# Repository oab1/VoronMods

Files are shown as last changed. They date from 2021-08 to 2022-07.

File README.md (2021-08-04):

# V2 Exhaust Housing (Re-circulating)
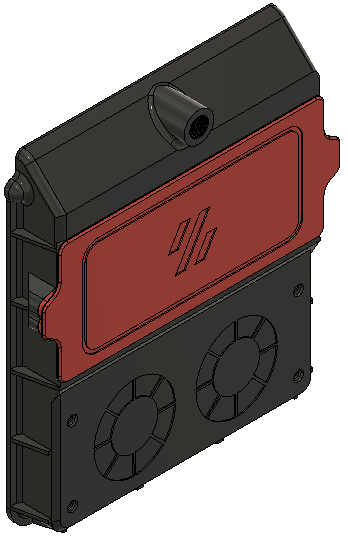
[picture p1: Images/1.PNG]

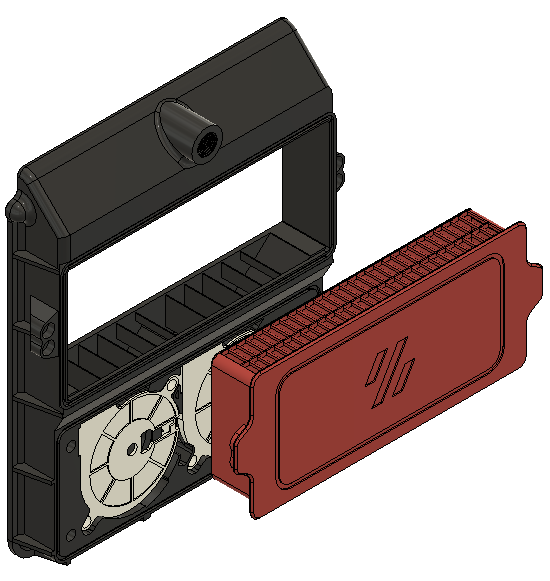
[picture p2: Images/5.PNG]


Modified existing v2.2 exhaust housing to incorporate u/0ndsk4's Nevermore micro re-circulating design. Added BSP fitting for bowden tube from v2.4 and a removable drawer as a filter basket to hold carbon pellets for filtration.

Uses the same 2 5015 Blower fans from the Nevermore, and 4mm activated carbon pellets. Two holes need to be cut into the back panel (1.5" diameter) for the blower fan inlets. The housing works as a good template once it is printed. Housing attaches to back panel with VHB tape, same as v2.2/2.4 designs. Pellets need to be replaced every so often, have heard anywhere from 50-100 hours. Have not run that long myself yet.

## Hardware needed:
- 2x 5015 blower fans (confirmed fitment with Winsin brand, but same as used in nevermore micro)
- 4x 6x3mm magnet (same as used in V2 BOM)
- 6x M3x5x4 heatset inserts
- 4x m3 screws (6-8mm length OK)
- 3M VHB tape
- Approx 200g of 4mm activated carbon pellets, I bought mine here:
https://envirosupply.net/products/4mm-pellet-virgin-coal-activated-carbon-charcoal-for-vapor-filtration-1-lb-bag

## Nevermore micro:
Based on original design from 0ndsk4:
https://github.com/0ndsk4/VoronUsers/tree/0ndsk4/printer_mods/0ndsk4/Nevermore_Air_Filter/Nevermore_Micro

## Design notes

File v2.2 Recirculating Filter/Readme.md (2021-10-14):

# Rear Panel Mounted Re-circulating Filter
Codename: FannyPack (a modified version of the Nevermore Micro Duo) 

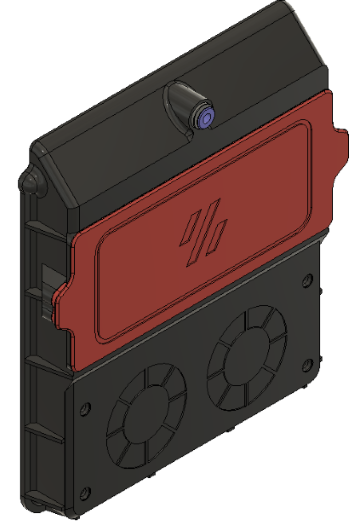
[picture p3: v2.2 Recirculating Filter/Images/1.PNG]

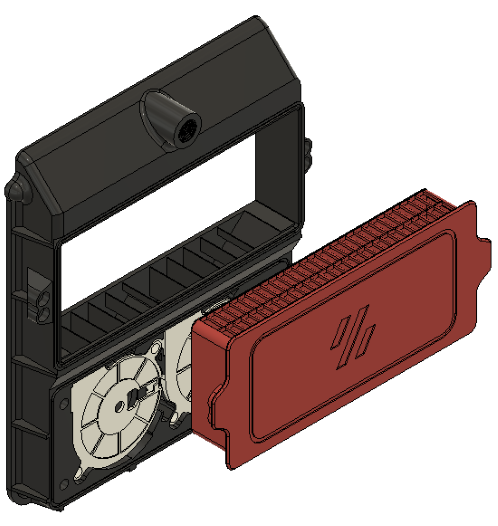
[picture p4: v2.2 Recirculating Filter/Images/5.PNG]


Modified existing v2.2 exhaust housing to incorporate u/0ndsk4's Nevermore Micro Duo:
- Uses the same 2 5015 Blower fans and 4mm activated carbon pellets. 
- Two holes need to be cut into the back panel (1.5" diameter) for the blower fan inlets. 
- The housing works as a good cutting template once it is printed. 
- Housing attaches to back panel with VHB tape
- Removable drawer as a filter basket to hold carbon pellets for filtration.
- Two fitting options for bowden tube: (1) 1/8" BSP adapter (2) EASUN Push Fitting adapter

I recommend printing the housing with at least 3 perimeters and about 15% infill. More infill than that is pretty overkill.

## Hardware needed:
- 2x 5015 blower fans (confirmed fitment with Winsin brand, but same as used in nevermore micro)
- 4x 6x3mm magnet (same as used in V2 BOM)
- 6x M3x5x4 heatset inserts
- 4x m3 screws (6-8mm length OK)
- 3M VHB tape
- Approx 200g of 4mm activated carbon pellets, I bought mine here:
https://envirosupply.net/products/4mm-pellet-virgin-coal-activated-carbon-charcoal-for-vapor-filtration-1-lb-bag

## Nevermore micro:
Based on original design from 0ndsk4:
https://github.com/0ndsk4/VoronUsers/tree/0ndsk4/printer_mods/0ndsk4/Nevermore_Air_Filter/Nevermore_Micro

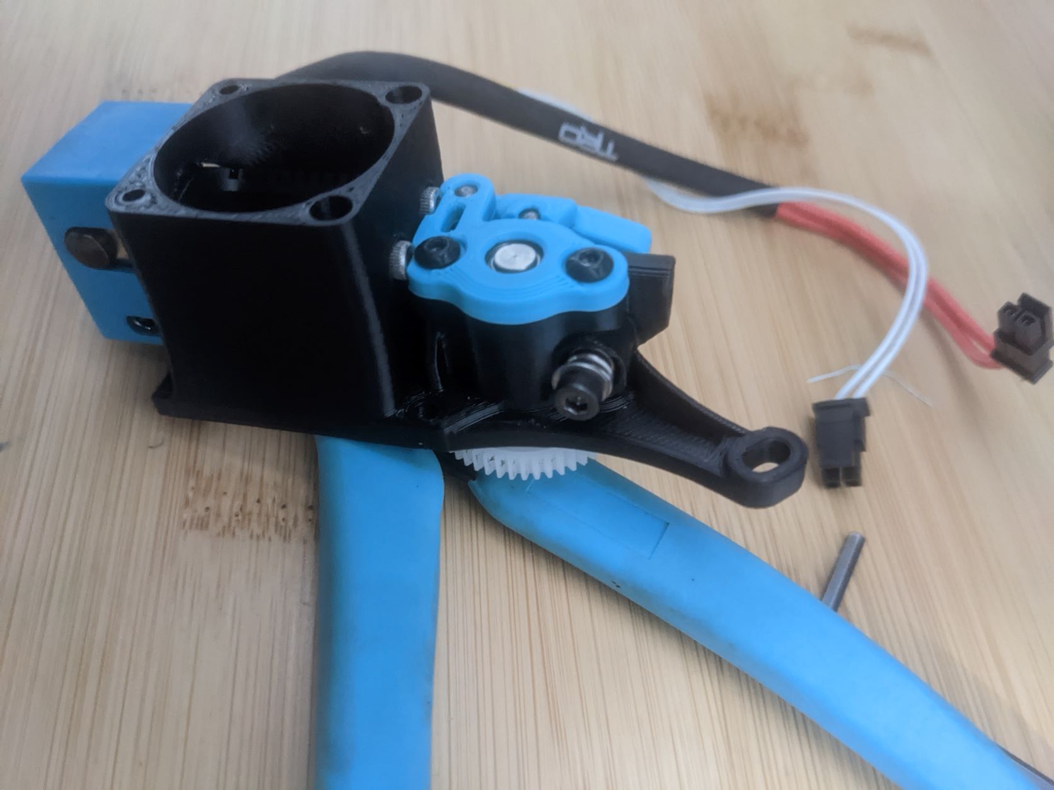
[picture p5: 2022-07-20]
v2.2 Recirculating Filter/Images/PXL_20220714_225406142.MP.jpg

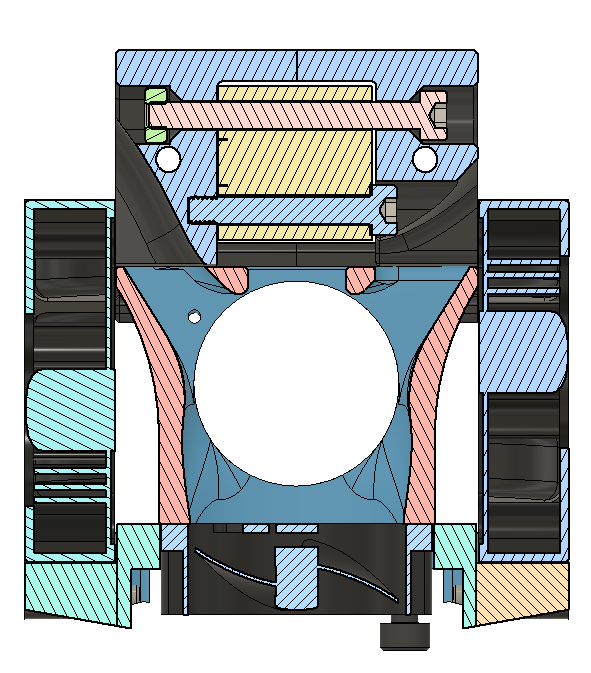
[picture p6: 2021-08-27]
v2.2 Sherpa Mini Toolhead/Images/v1/Exhaust Flow Path.PNG

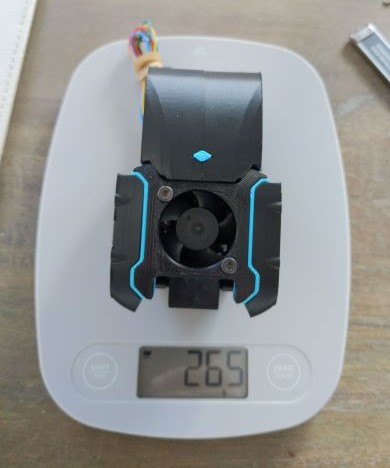
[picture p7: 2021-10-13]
v2.2 Sherpa Mini Toolhead/Images/scale_weight.PNG

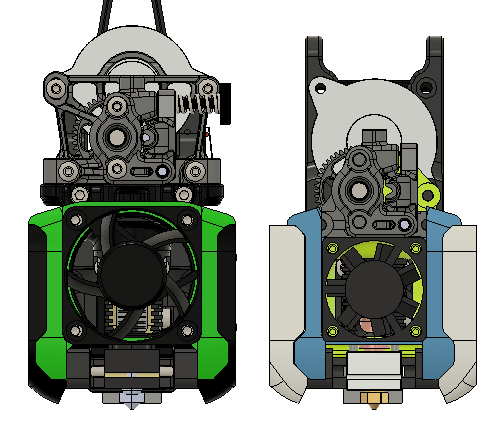
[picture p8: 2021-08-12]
v2.2 Sherpa Mini Toolhead/Images/v1/size compare.png

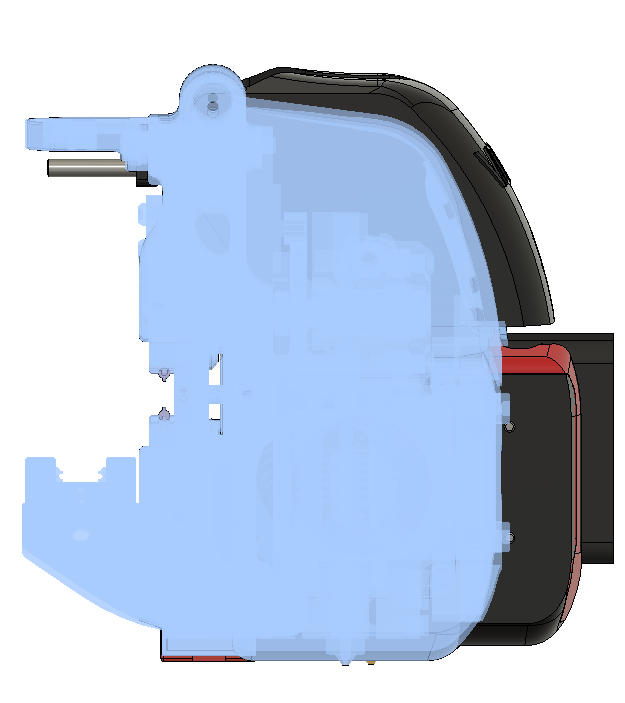
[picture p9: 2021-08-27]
v2.2 Sherpa Mini Toolhead/Images/size compare 2p2 original.PNG

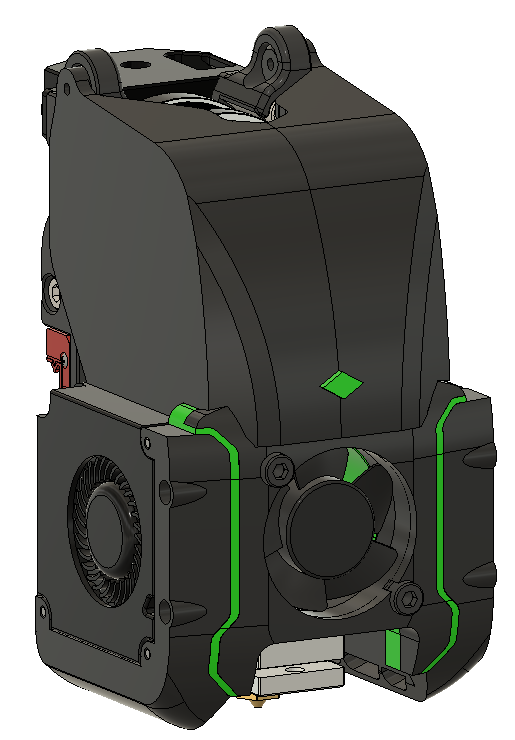
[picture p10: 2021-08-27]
v2.2 Sherpa Mini Toolhead/Images/v1/annex-green.PNG

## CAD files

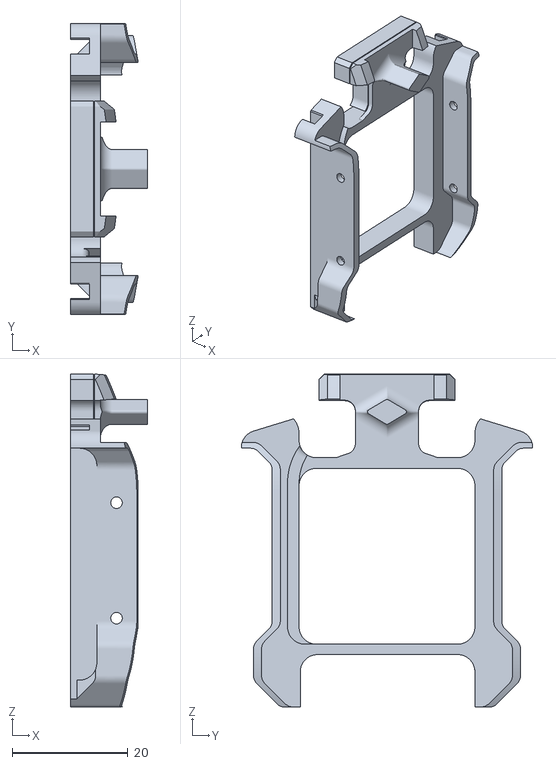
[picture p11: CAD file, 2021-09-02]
v2.2 Sherpa Mini Toolhead/STL/fan_back_plate.stl
13.3 x 50.4 x 57.6

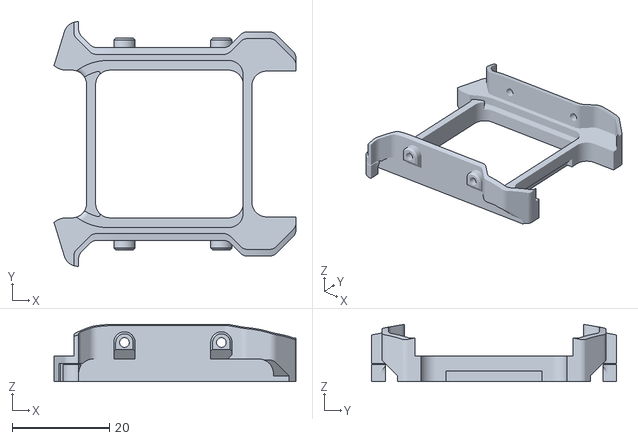
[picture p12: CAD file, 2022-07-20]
v2.2 Toolhead/STL/Tronhead RC2/annex redoubt + huvud specific/fan_back_plate.stl
49.8 x 50.4 x 11.8

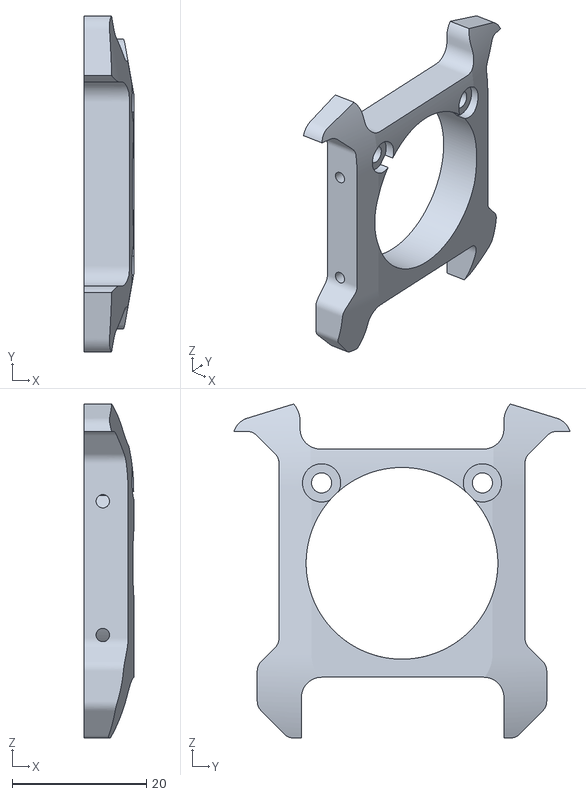
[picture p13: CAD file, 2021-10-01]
v2.2 Toolhead/STL/Tronhead RC2/annex redoubt specific/fan_front_plate.stl
7.39 x 50.1 x 49.8

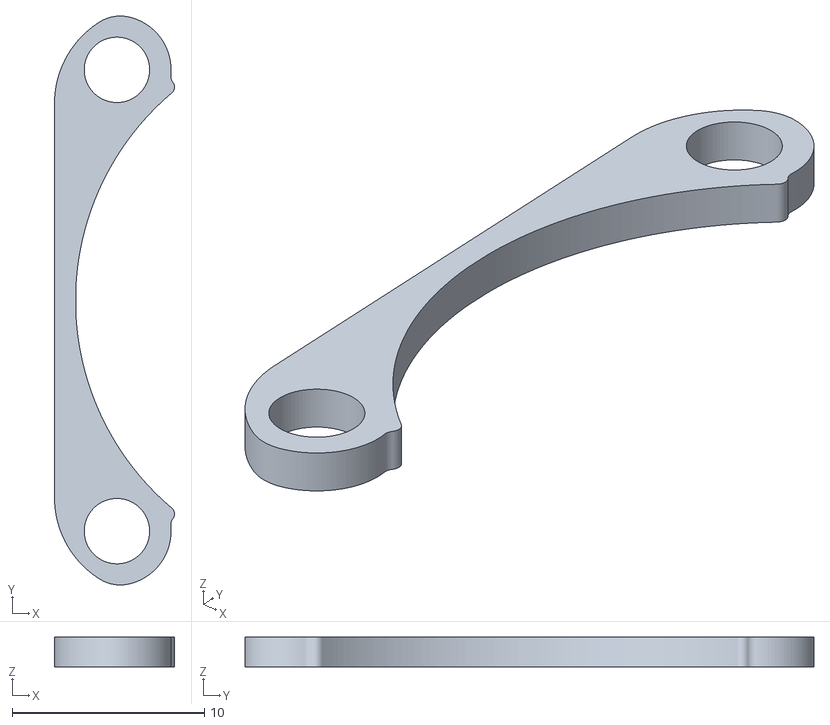
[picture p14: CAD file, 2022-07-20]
v2.2 Toolhead/STL/Tronhead RC2/spacer.stl
6.25 x 29.6 x 1.55

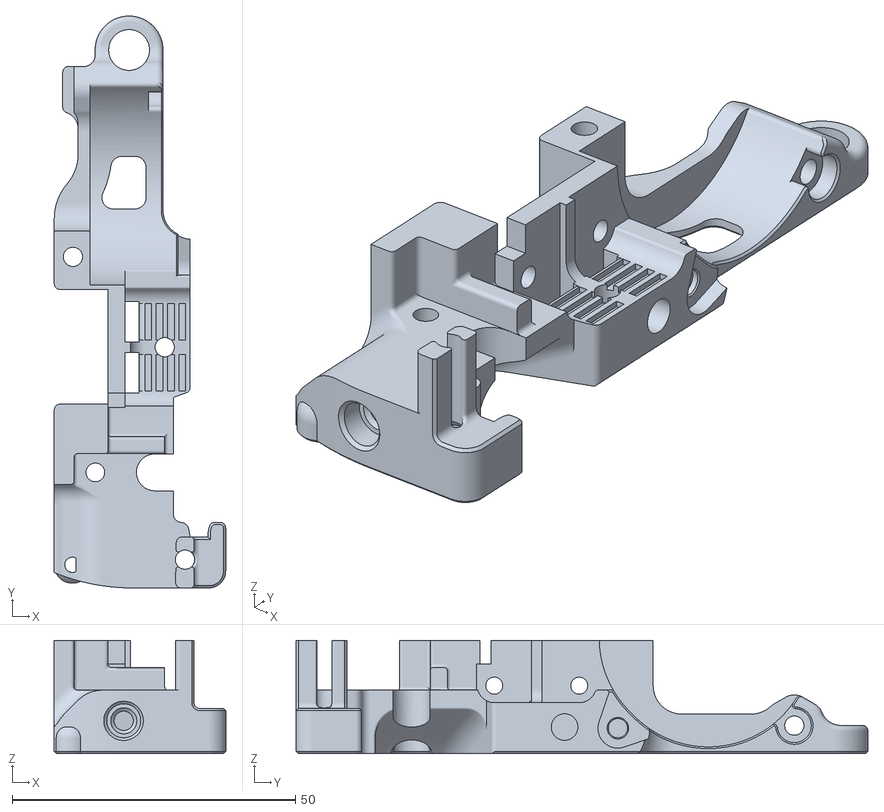
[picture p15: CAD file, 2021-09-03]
v2.2 Toolhead/STL/Tronhead RC2/voron 2.4 specific/x-carriage-omron-mgn9h-single (R).stl
30.3 x 100.9 x 20.0

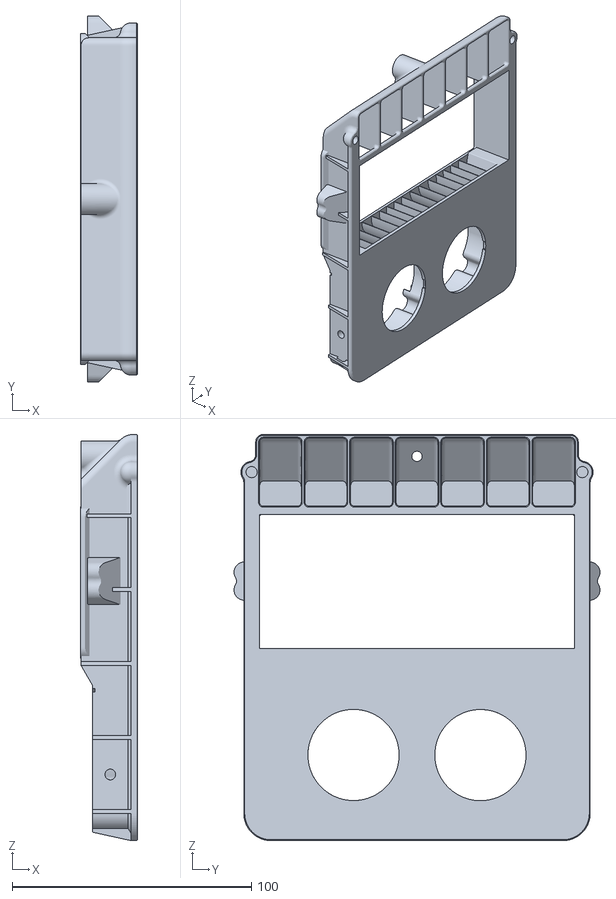
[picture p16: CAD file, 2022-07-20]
v2.2 Recirculating Filter/STL/Housing_rev2 (PushFitting).stl
23.7 x 152.9 x 169.8

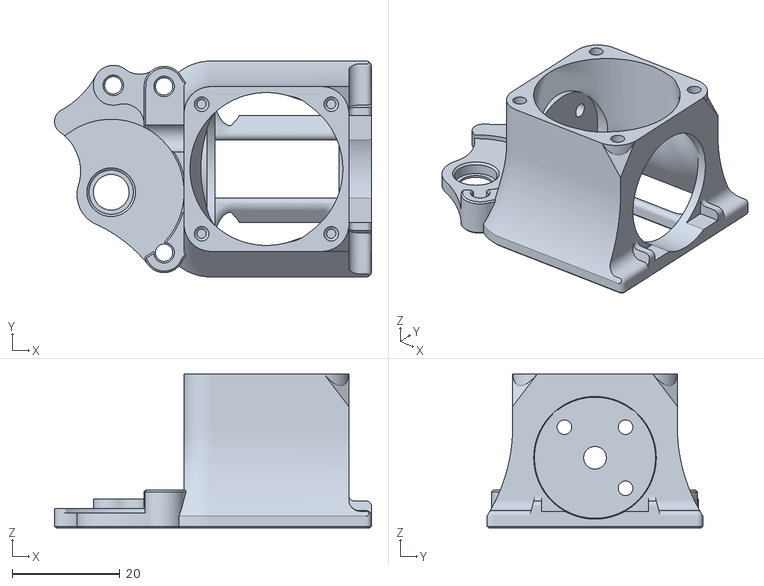
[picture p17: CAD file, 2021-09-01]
v2.2 Sherpa Mini Toolhead/STL/Toolhead Mount_rev2.stl
58.7 x 40.0 x 28.5

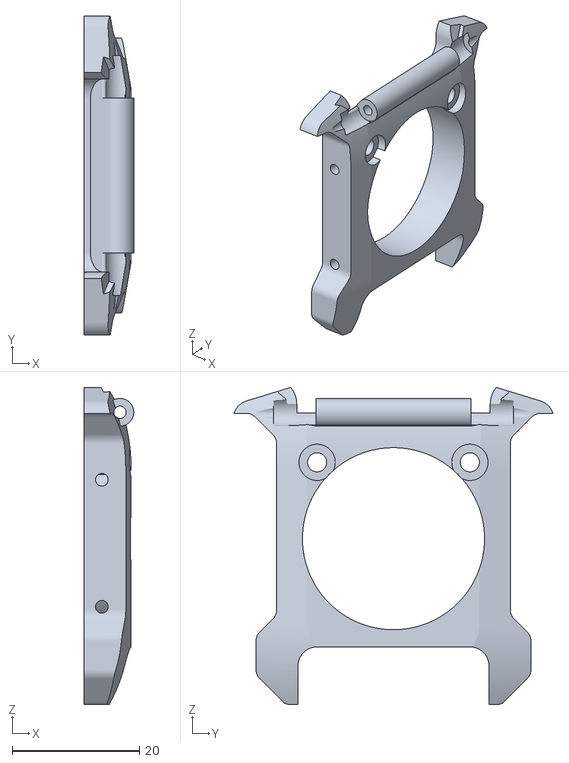
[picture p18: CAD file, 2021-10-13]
v2.2 Toolhead/STL/Tronhead RC2/annex redoubt + huvud specific/fan_front_plate.stl
7.78 x 50.1 x 49.8

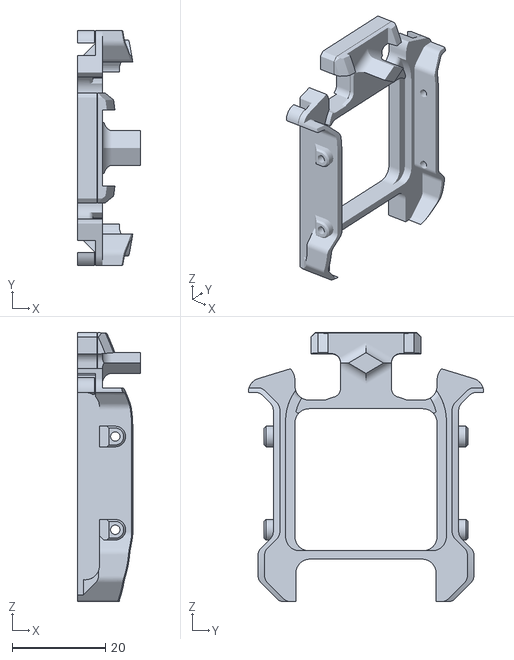
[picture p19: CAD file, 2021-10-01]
v2.2 Toolhead/STL/Tronhead RC2/annex redoubt specific/[a]_fan_back_plate.stl
13.4 x 50.4 x 57.6

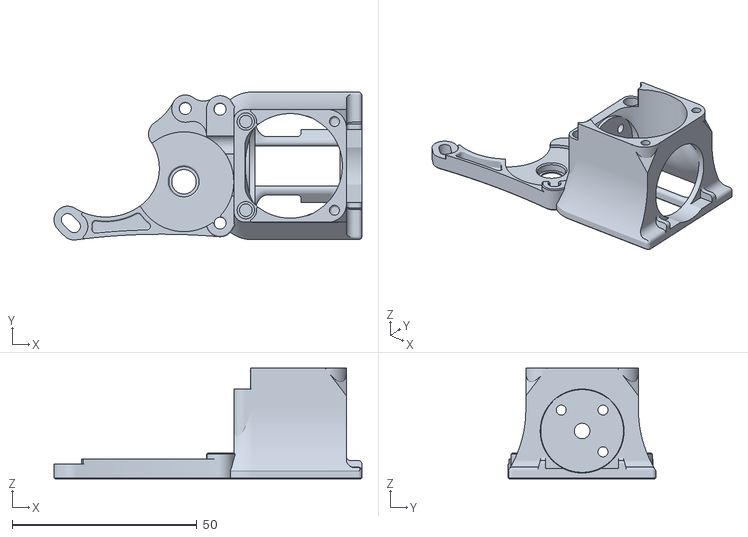
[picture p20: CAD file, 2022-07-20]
v2.2 Toolhead/STL/Tronhead RC2/Toolhead Mount.stl
83.4 x 40.1 x 30.1

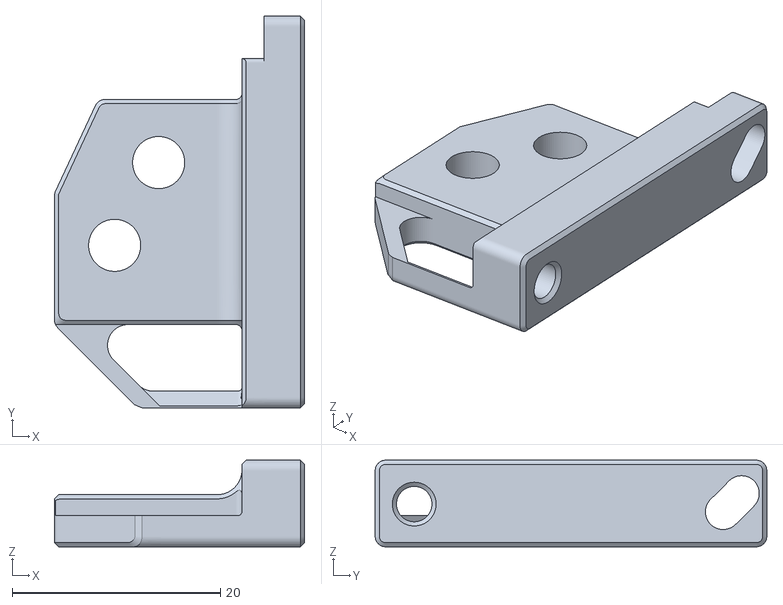
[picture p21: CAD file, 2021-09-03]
v2.2 Toolhead/STL/Tronhead RC2/voron 2.4 specific/1011_china_chain_mount.stl
24.0 x 37.6 x 8.32

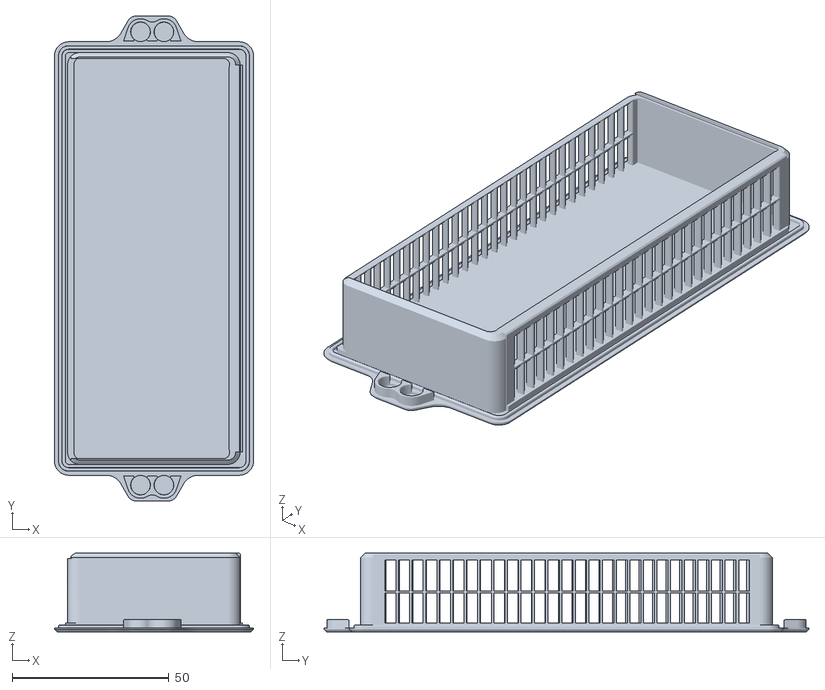
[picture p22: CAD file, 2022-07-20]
v2.2 Recirculating Filter/STL/Basket.stl
63.5 x 154.7 x 25.1

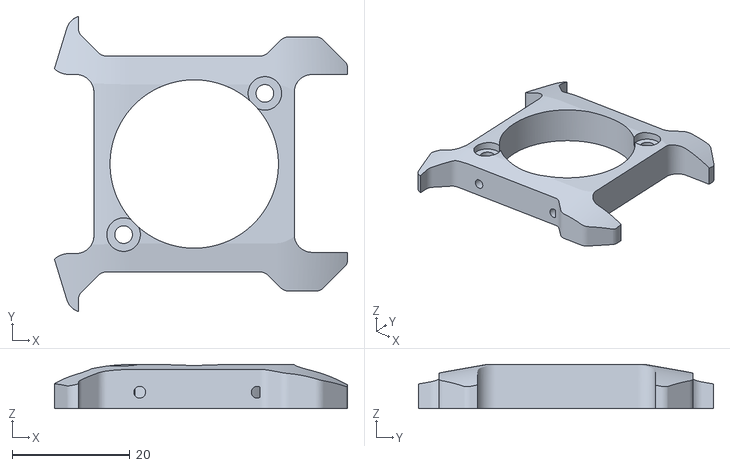
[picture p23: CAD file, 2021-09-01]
v2.2 Sherpa Mini Toolhead/STL/fan_cover_plate.stl
49.8 x 50.1 x 7.49

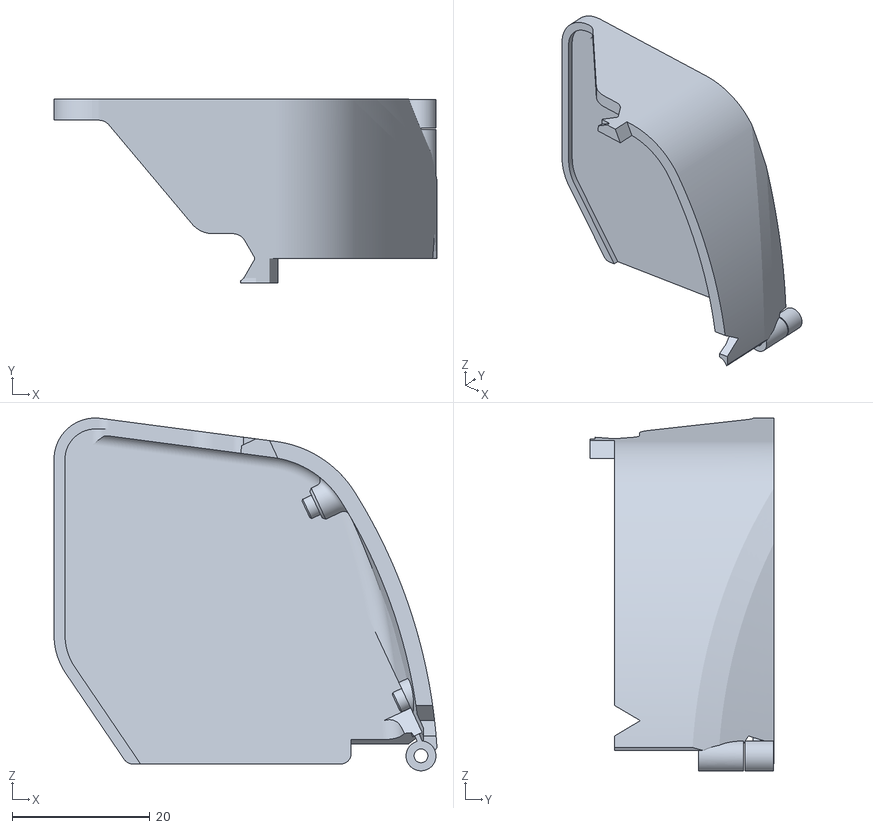
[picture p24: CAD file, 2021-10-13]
v2.2 Toolhead/STL/Tronhead RC2/annex redoubt + huvud specific/Connector_Cover_Right.stl
55.7 x 26.8 x 51.3

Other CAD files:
v2.2 Toolhead/STL/Tronhead RC2/annex redoubt specific/X-Carriage_Left (redoubt umbilical).stl
v2.2 Toolhead/STL/Tronhead RC2/Cooling Fan Duct Right.stl
v2.2 Toolhead/STL/Tronhead RC2/voron 2.4 specific/IGUS_chain_mount.stl
v2.2 Recirculating Filter/STL/Cap.stl
v2.2 Recirculating Filter/STL/Cover.stl
v2.2 Recirculating Filter/STL/Housing_rev1 (PushFitting).stl
v2.2 Recirculating Filter/STL/Plate.stl
v2.2 Toolhead/STL/Tronhead RC2/Cooling Fan Duct Left.stl
v2.2 Toolhead/STL/Tronhead RC2/annex redoubt + huvud specific/Connector_Cover_Left.stl
v2.2 Toolhead/STL/Tronhead RC2/annex redoubt + huvud specific/X-Carriage_Left.stl
v2.2 Toolhead/STL/Tronhead RC2/annex redoubt + huvud specific/X-Carriage_Right.stl
v2.2 Toolhead/STL/Tronhead RC2/annex redoubt specific/Connector_Cover_Left.stl
v2.2 Toolhead/STL/Tronhead RC2/annex redoubt specific/Connector_Cover_Right.stl
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

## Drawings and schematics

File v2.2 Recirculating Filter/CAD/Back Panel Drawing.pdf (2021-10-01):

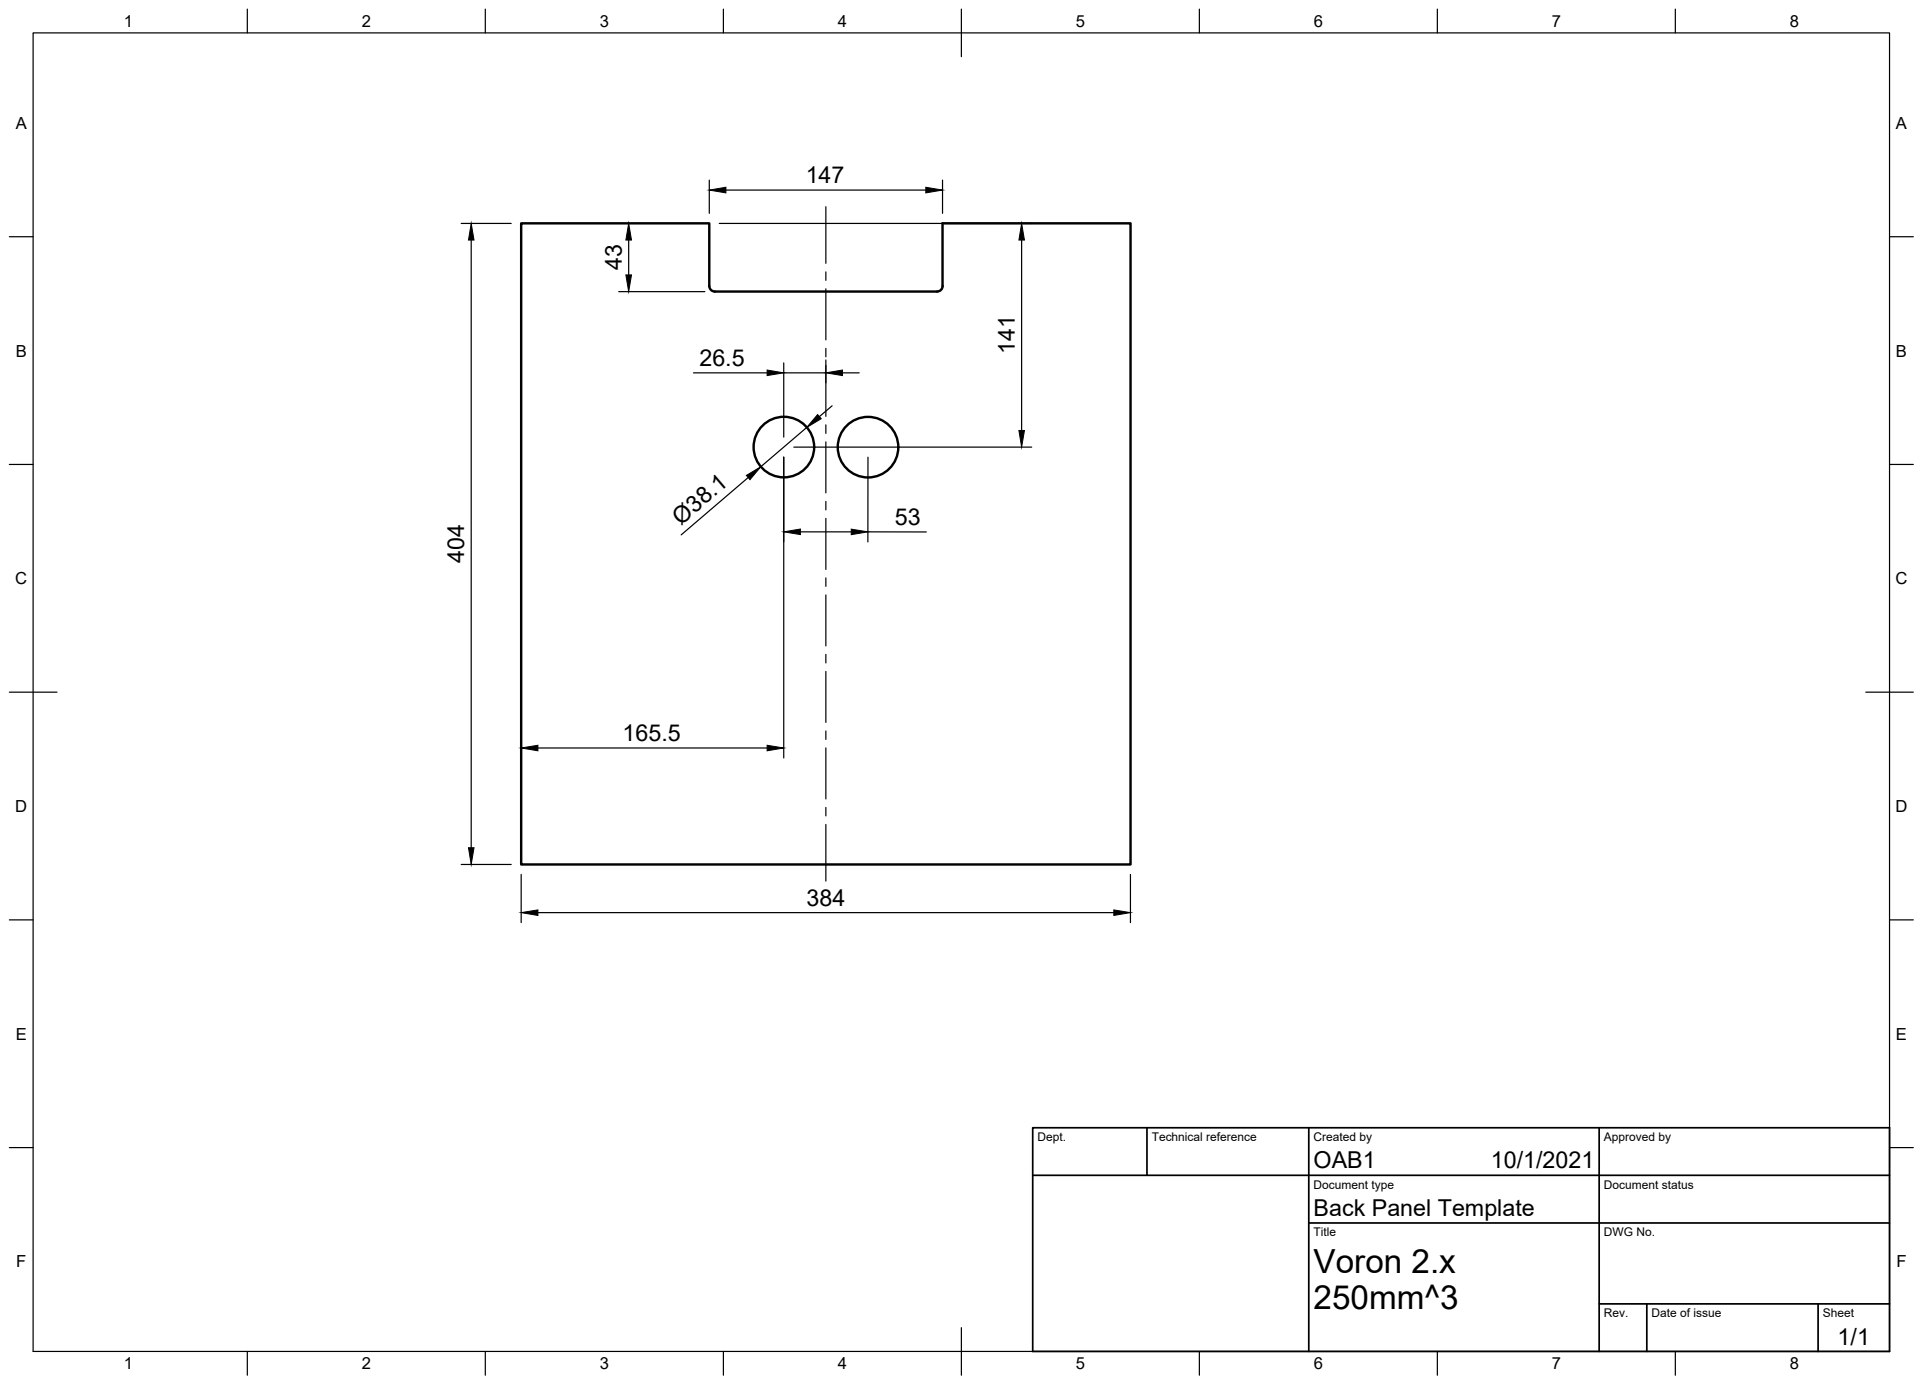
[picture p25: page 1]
Title; DWG No.; Rev.; Date of issue; Sheet; Voron 2.x; OAB1 141

Dept. | Technical reference | Created by 10/1/2021 | Approved by

Document type Back Panel Template | Document status

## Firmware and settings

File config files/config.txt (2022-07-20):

# For more options and information see
# http://rpf.io/configtxt
# Some settings may impact device functionality. See link above for details

# uncomment if you get no picture on HDMI for a default "safe" mode
#hdmi_safe=1

# uncomment this if your display has a black border of unused pixels visible
# and your display can output without overscan
#disable_overscan=1

# uncomment the following to adjust overscan. Use positive numbers if console
# goes off screen, and negative if there is too much border
#overscan_left=16
#overscan_right=16
#overscan_top=16
#overscan_bottom=16

# uncomment to force a console size. By default it will be display's size minus
# overscan.
#framebuffer_width=1280
#framebuffer_height=720

# uncomment if hdmi display is not detected and composite is being output
#hdmi_force_hotplug=1

# uncomment to force a specific HDMI mode (this will force VGA)
#hdmi_group=1
#hdmi_mode=1

# uncomment to force a HDMI mode rather than DVI. This can make audio work in
# DMT (computer monitor) modes
#hdmi_drive=2

# uncomment to increase signal to HDMI, if you have interference, blanking, or
# no display
#config_hdmi_boost=4

# uncomment for composite PAL
#sdtv_mode=2

#uncomment to overclock the arm. 700 MHz is the default.
#arm_freq=800

# Uncomment some or all of these to enable the optional hardware interfaces
#dtparam=i2c_arm=on
#dtparam=i2s=on
#dtparam=spi=on

# Uncomment this to enable infrared communication.
#dtoverlay=gpio-ir,gpio_pin=17
#dtoverlay=gpio-ir-tx,gpio_pin=18

# Additional overlays and parameters are documented /boot/overlays/README

# Enable audio (loads snd_bcm2835)
dtparam=audio=on

[pi4]
# Enable DRM VC4 V3D driver on top of the dispmanx display stack
dtoverlay=vc4-fkms-v3d
max_framebuffers=2

[all]
#dtoverlay=vc4-fkms-v3d
# enable raspicam
start_x=1
gpu_mem=128

# For Raspberry Pi CAN Hat
dtoverlay=mcp2515-can0,oscillator=12000000,interrupt=25

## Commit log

2021-08-12 Rename 2.2 Recirculating Filter/temp to v2.2 Recirculating Filter/temp
2021-08-12 Rename 2.2 Sherpa Mini Toolhead/temp to v2.2 Sherpa Mini Toolhead/temp
2021-08-12 Update and rename README.md to v2.2 Recirculating Filter/Readme.md
2021-08-12 Moved 2.2 Exhaust to subfolder
    [2p2 Exhaust + Nevermore Micro.f3d, Basket.stl, Cap.stl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]
2021-08-12 Added fillets to filter basket, beefed up o-ring gland on housing
    [Basket.stl]
2021-08-12 Updated CAD model and notes
    [2p2 Exhaust + Nevermore Micro.f3d, Fanny Pack v1.f3d]
2021-08-12 Upload initial files
    [Toolhead Mount.stl]
2021-08-12 First push
    generate toolhead mount stl
    [Toolhead Mount v1.stl, Toolhead Mount.stl]
2021-08-12 upload x-carriage
    [x-carriage-LHS.stl, x-carriage-RHS.stl]
2021-08-12 add sherpa mini modifications
    [sherpa_mini_body_modified.stl]
2021-08-13 Update Cover.stl
    Fixed hole sizes for m3 x 6mm screw, added chamfer
    [Cover.stl]
2021-08-13 Update housing magnet press fit hole size (was too loose)
2021-08-15 Create Tronhead v2.f3d
    completed fan assembly
2021-08-16 Finished cooling ducts
2021-08-16 updated cooling duct mod STLs
    [Cooling Fan Duct Left.stl, Cooling Fan Duct Right.stl, Toolhead Mount v1.stl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]
2021-08-17 New Carriages
    [Toolhead Mount v3.stl, x-carriage-LHS-omron.stl, x-carriage-LHS.stl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]
2021-08-17 Fixed interference with silicone sock
    [Cooling Fan Duct - Left.stl, Cooling Fan Duct - Right.stl, Cooling Fan Duct Left.stl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]
2021-08-19 wire routing channel for LDO stepper
    [x-carriage-omron (L).stl, x-carriage-omron (R).stl]
2021-08-19 remove old carriages
    [1011_china_chain_mount.stl, x-carriage-LHS-omron.stl, x-carriage-RHS-omron.stl]
2021-08-21 remove old files
    [Front_Plate.stl, Toolhead Mount.stl]
2021-08-21 Updated model with correct fasteners and placements
    [sherpa_mini_body_flipped_tensioner.stl, sherpa_mini_body_mod.stl, sherpa_mini_body_modified.stl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]
2021-08-21 update CAD
2021-08-21 Update sherpa_mini_idler_arm (flipped).stl
    [sherpa_mini_idler_arm (flipped).stl]
2021-08-27 New v2 with cosmetic updates and pulled fan 5mm closer to hotend
    [Connector_Cover_Left.stl, Connector_Cover_Right.stl, Cooling Fan Duct - Left.stl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]
2021-08-27 added fillets to connect cover
    [Connector_Cover_Left.stl, Connector_Cover_Right.stl]
2021-08-29 Updated fanny pack STL For push fitting, updated 2.2 toolhead for new cover
    [Connector_Cover_Left.stl, Housing_rev1 (PushFitting).stl, fan_back_plate.stl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]
2021-08-30 update BSP adapter housing, f3d export
    [Fanny Pack v1.f3d, Housing_rev1 (PushFitting).stl]
2021-09-01 update STL's for clearance issues
    [Connector_Cover_Left.stl, Connector_Cover_Right.stl, Cooling Fan Duct - Left.stl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]
2021-09-01 Fix print orientation in STL's
    [1011_china_chain_mount.stl, Connector_Cover_Left.stl, Connector_Cover_Right.stl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]
2021-09-01 Update Toolhead Mount_rev2.stl
    [Toolhead Mount_rev2.stl]
2021-09-01 Update CAD, left cover print orientation
    [Connector_Cover_Left.stl]
2021-09-01 adjustments for x endstop
    [Toolhead Mount_rev2.stl, x-carriage-omron (L)_rev2.stl, x-carriage-omron (R)_rev2.stl]
2021-09-02 new reinforced sherpa mount
    [Toolhead Mount_rev3.stl, Tronhead_Sherpa Girdle v1.stl, fan_back_plate.stl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]
2021-09-02 updates for reinforced sherpa front cover and wire routing
    [Toolhead Mount_rev2.stl, fan_back_plate.stl, fan_back_plate_rev1.stl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]
2021-09-03 release candidate 1 - everything works!
    rc1 file updates with correct print orientations
    [1011_china_chain_mount.stl, Connector_Cover_Left.stl, Connector_Cover_Right.stl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]
2021-09-10 Create Tronhead RC1 (redoubt carriage) v1.step
2021-09-15 Added redoubt dual mgn9 x-carriage assembly
    [1011_china_chain_mount.stl, Cable_Clamp.stl, IGUS_chain_mount.stl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]
2021-09-17 added XY joints (belts moved 2mm closer to extrusion)
    [XY Joint - Left - Bottom.stl, XY Joint - Left - Top.stl, XY Joint - Right - Bottom.stl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]
2021-10-01 Add pdf to Fanny pack for cutouts, Start new tronhead RC2 (huvud toolhead PCB) version
    [Cooling Fan Duct Left.stl, Cooling Fan Duct Right.stl, Toolhead Mount_rc1_v2.stl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]
2021-10-13 Update RC2 files
    [1011_china_chain_mount.stl, Cable_Clamp.stl, Connector_Cover_Left.stl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]
2021-10-14 Updated alternate configs (1 = voron 2.4, 2 = redoubt, 3 = huvud)
    [1011_china_chain_mount.stl, Connector_Cover_Left.stl, Connector_Cover_Right.stl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]
2022-07-20 New version for Tronhead, RC3
    [Basket.stl, Cap.stl, Connector_Cover_Left (new).stl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]
2022-07-20 update images
    [1011_china_chain_mount.stl, Connector_Cover_Left (new).stl, Connector_Cover_Left.stl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]
2022-07-20 Update folder structure, names
    [1011_china_chain_mount.stl, Connector_Cover_Left (new).stl, Connector_Cover_Left.stl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]
2022-07-20 Name change
    [1011_china_chain_mount.stl, Connector_Cover_Left (new).stl, Connector_Cover_Left.stl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]
2022-07-20 Create One-piece mount.png
2022-08-24 RC3 final updates
    [1011_china_chain_mount.stl, Connector_Cover_Left (new).stl, Connector_Cover_Left.stl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]
